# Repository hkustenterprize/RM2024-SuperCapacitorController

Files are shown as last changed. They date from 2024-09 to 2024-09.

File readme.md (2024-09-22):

# 香港科技大学ENTERPRIZE战队
# RM2024超级电容控制器
# 硬件方案&软件方案 完全开源

>设计者：蒋益诚 戎羿
> 
>文档撰写：戎羿

## 文件结构

```
Calibration/cal.xlsx                              ----校准用Excel工具表
Core                                              ----核心代码文件
Docs                                              ----文档附图源码
Drivers                                           ----STM32驱动文件
hardware                                          ----硬件项目文件
      --    SuperCap2024_Control_V1.1R_F3_ISOPWR  ----控制板Kicad项目文件
      --    SuperCap2024_Power_V1.2R              ----功率板Kicad项目文件
Middlewares/ST/ARM/DSP/Inc/arm_math.h             ----数学加速库头文件
.clang-format
.clang-tidy
.cproject
CMakeLists.txt                                    ----由CLion生成的CMake编译文件，便于CLion创建项目
CMakeLists_template.txt
Makefile                                          ----由CubeMX生成的MakeFile编译文件
RM2024-SuperCap-F3-V0.2.ioc                       ----STM32CubeMX项目文件
startup_stm32f334x8.s                             ----由CubeMX生成的启动文件
startup_stm32f334x8_SuperCap.s                    ----由CubeMX生成的启动文件改版，当前使用中
STM32F334R8Tx_FLASH.ld                            ----由CubeMX生成的链接文件
STM32F334R8Tx_SuperCap_FLASH.ld                   ----由CubeMX生成的链接文件改版，当前使用中
SuperCap-F3.mk                                    ----队内通用MakeFile库
```

## 使用方法
###	硬件接口&连接
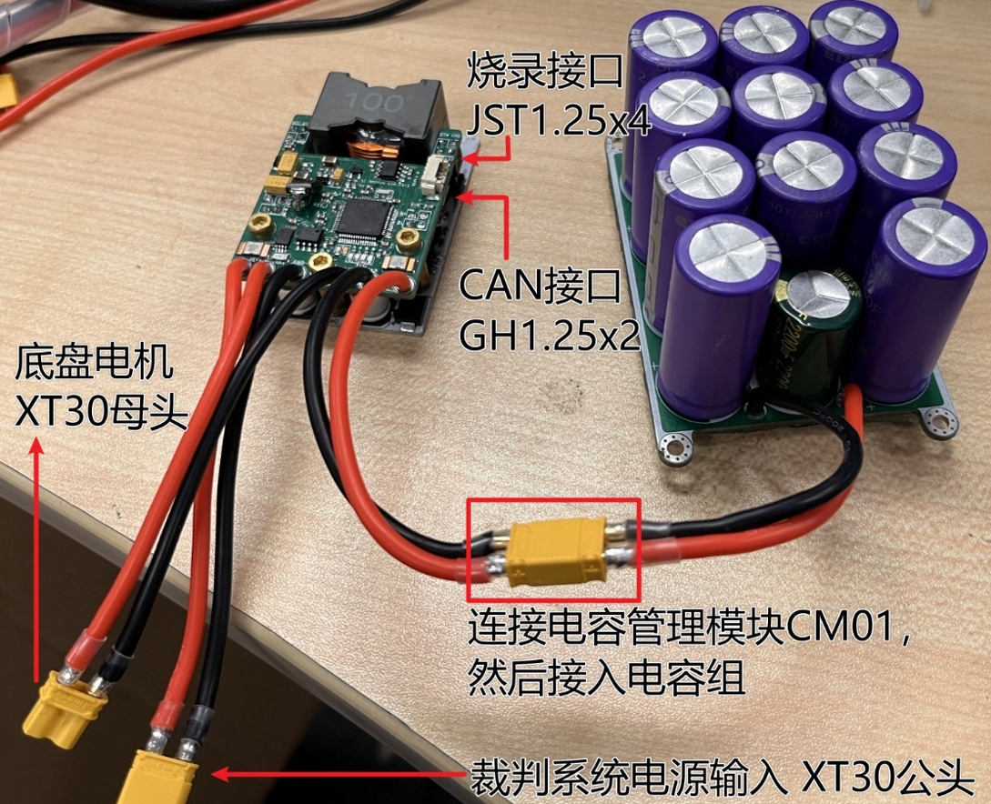
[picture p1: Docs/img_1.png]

###	软件环境&编译&烧录
本项目基于GCC ARM GNU工具链。
1.	安装GCC环境。以Windows系统下为例，下载MSYS2并安装，在系统环境变量中加入相关目录。
2.	安装`arm-none-eabi-gcc`
      然后即可执行编译操作。需要注意编译时需要指定HARDWARE_ID，否则将会报错。

      `make -j HARDWARE_ID=xxx`

      得到`build/`目录下`RM2024-SuperCap-F3-V1R.elf`文件即为编译成功。

      将elf文件在ozone新建项目中打开，即可通过JLink烧录至MCU中。

## 移植兼容性
该项目通过STM32的HAL库实现大部分去耦，方便移植。

用户代码全部位于 `Core/` 中，将相应文件转移到另生成的项目中可以轻松移植。例如专用STM32G474作为开发用MCU。

而部分相对底层的外设代码，例如HRTIM与ADC的配置等，则需要手动修改。

总体而言该项目可移植性较佳。

## 开源报告
可以见于Github Release处

## 开源说明
本项目通过GPL3.0协议开源

## PCB项目说明
硬件部分使用KiCAD设计。

Github上在线预览：使用[KiCanvas](https://kicanvas.org/)

上板原理图：[预览](https://kicanvas.org/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)

上板PCB：[预览](https://kicanvas.org/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)

下板原理图：[预览](https://kicanvas.org/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)

下板PCB：[预览](https://kicanvas.org/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)

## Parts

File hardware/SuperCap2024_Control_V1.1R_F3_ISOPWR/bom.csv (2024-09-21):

Designator | Footprint | Quantity | Value | LCSC Part #
BZ1 | MLT-9032 | 1 | Buzzer-9032
C1, C10, C11, C12, C13, C14, C17, C19, C20, C21, C22, C23, C24, C25, C26, C27, C28, C29, C30, C31, C32, C33, C39, C41, C47, C8 | 0603 | 26 | 100n
C15, C16, C3, C34, C40, C42, C5 | 0603 | 7 | 10u
C18, C36, C37, C44, C45, C49, C50, C52, C53, C54, C55, C9 | 1206 | 12 | 10u
C38, C46 | CP_EIA-6032-28_Kemet-C | 2 | C_Polarized
C4 | 0603 | 1 | 20p
C43 | 0603 | 1 | 10n
C51, C56, C57, C58 | 1206 | 4 | 100u 6.3V
D1, D2, D3 | D_SMF | 3 | DSS34
D10, D11, D19 | D_SMF | 3 | SMF10A
D13, D14, D6, D7, D8, D9 | 0603 | 6 | LED
D22 | D_SMF | 1 | SMF5V0A
D4 | D_SMF | 1 | SMF3.3A
D5 | D_SMA | 1 | SMAJ28A
F1, F2 | 1206 | 2 | 30A
F3, F4 | 1206 | 2 | 1A
FB1 | 1206 | 1 | FerriteBead
FB2 | 0603 | 1 | FerriteBead
H1, H2, H3 | MountingHole_3.2mm_M3_ISO14580_Pad | 3 | MountingHole_Pad
J1, J4 | PinHeader_2x02_P2.54mm_Vertical_SMD | 2 | Conn_02x02_Odd_Even
J2 | JST_GH_SM02B-GHS-TB_1x02-1MP_P1.25mm_Horizontal | 1 | Conn_01x02_MountingPin
J3 | Molex_PicoBlade_53261-0471_1x04-1MP_P1.25mm_Horizontal | 1 | Conn_01x04_MountingPin
J5, J6 | PinHeader_2x02_P2.54mm_Vertical | 2 | Conn_02x02_Odd_Even
L1 | L_Bourns-SRN4018 | 1 | 4.7u
L2 | L_Sunlord_SWPA252012S | 1 | 4.7u
Q1 | SOT-23 | 1 | AO3400A
R1, R2, R22, R23, R24, R26, R27, R3, R37, R4, R5 | 0603 | 11 | 33r
R10, R11, R7, R8 | 0603 | 4 | 2.2k
R12, R15, R9 | 2512 | 3 | 2mr
R13, R14, R30, R31 | 0603 | 4 | 1k
R16, R19 | 0603 | 2 | 90k 25ppm
R17, R20 | 0603 | 2 | 10k 25ppm
R18, R21 | 0603 | 2 | 68r
R25, R36, R38 | 0603 | 3 | 120r
R28, R40, R42, R6 | 0603 | 4 | 10k
R39 | 0603 | 1 | 118k
R41 | 0603 | 1 | 53.6k
TP1, TP2, TP3, TP4, TP5, TP6 | TestPoint_Plated_Hole_D3.0mm | 6 | TestPoint
U1, U3 | BxxxxS-1W | 2 | ISO_DC
U10 | SOT-23-5 | 1 | RS3236
U11, U9 | SOT-23-6 | 2 | RY8411
U2, U4, U5 | TSSOP-8_4.4x3mm_P0.65mm | 3 | INA240A1PW
U6 | SOIC-8_3.9x4.9mm_P1.27mm | 1 | GS8332-SR
U7 | LQFP-64_10x10mm_P0.5mm | 1 | STM32F334R8Tx
U8 | SOIC-8_3.9x4.9mm_P1.27mm | 1 | SIT1042/3
Y1 | Resonator_SMD_Murata_CSTxExxV-3Pin_3.0x1.1mm | 1 | CSTCE8M

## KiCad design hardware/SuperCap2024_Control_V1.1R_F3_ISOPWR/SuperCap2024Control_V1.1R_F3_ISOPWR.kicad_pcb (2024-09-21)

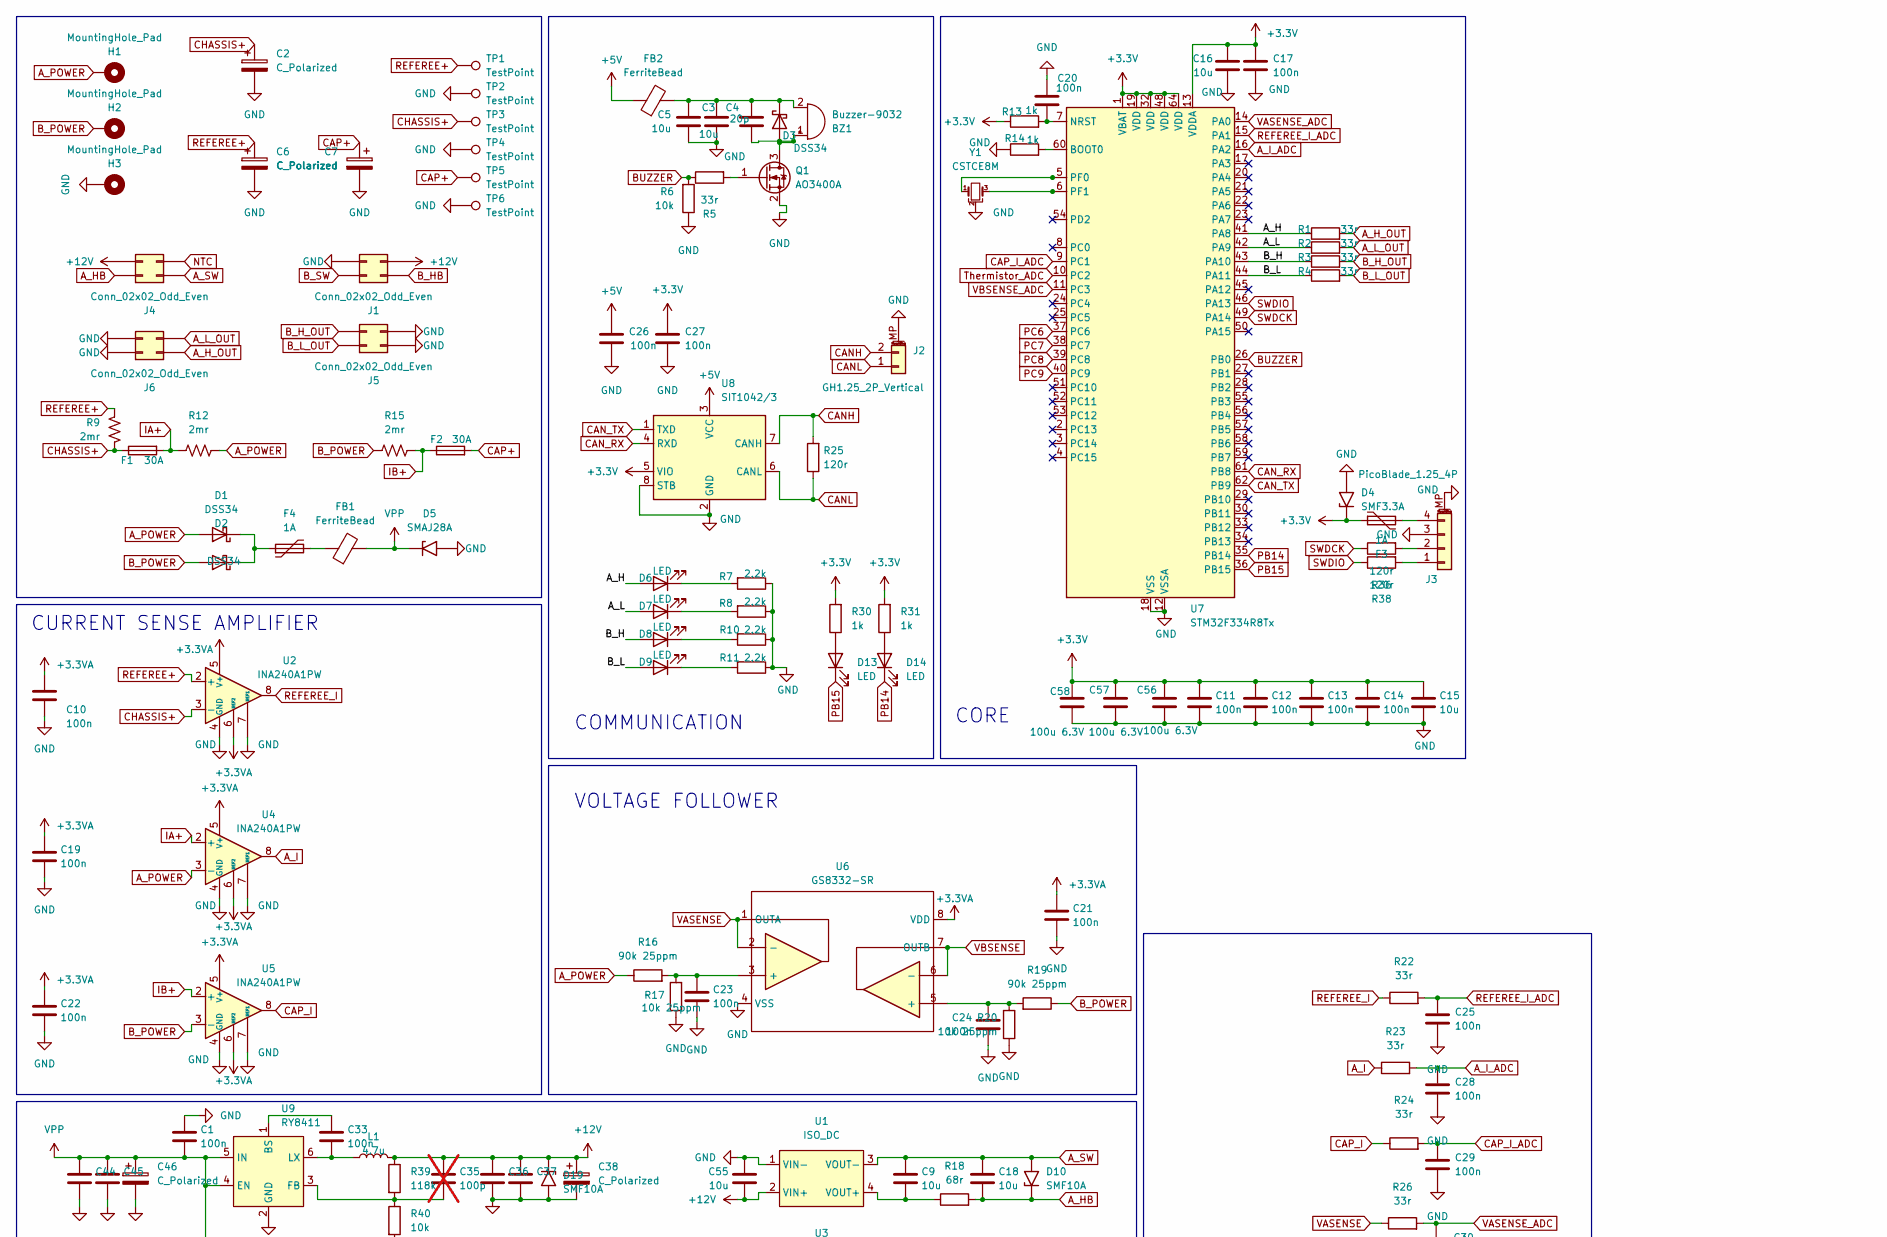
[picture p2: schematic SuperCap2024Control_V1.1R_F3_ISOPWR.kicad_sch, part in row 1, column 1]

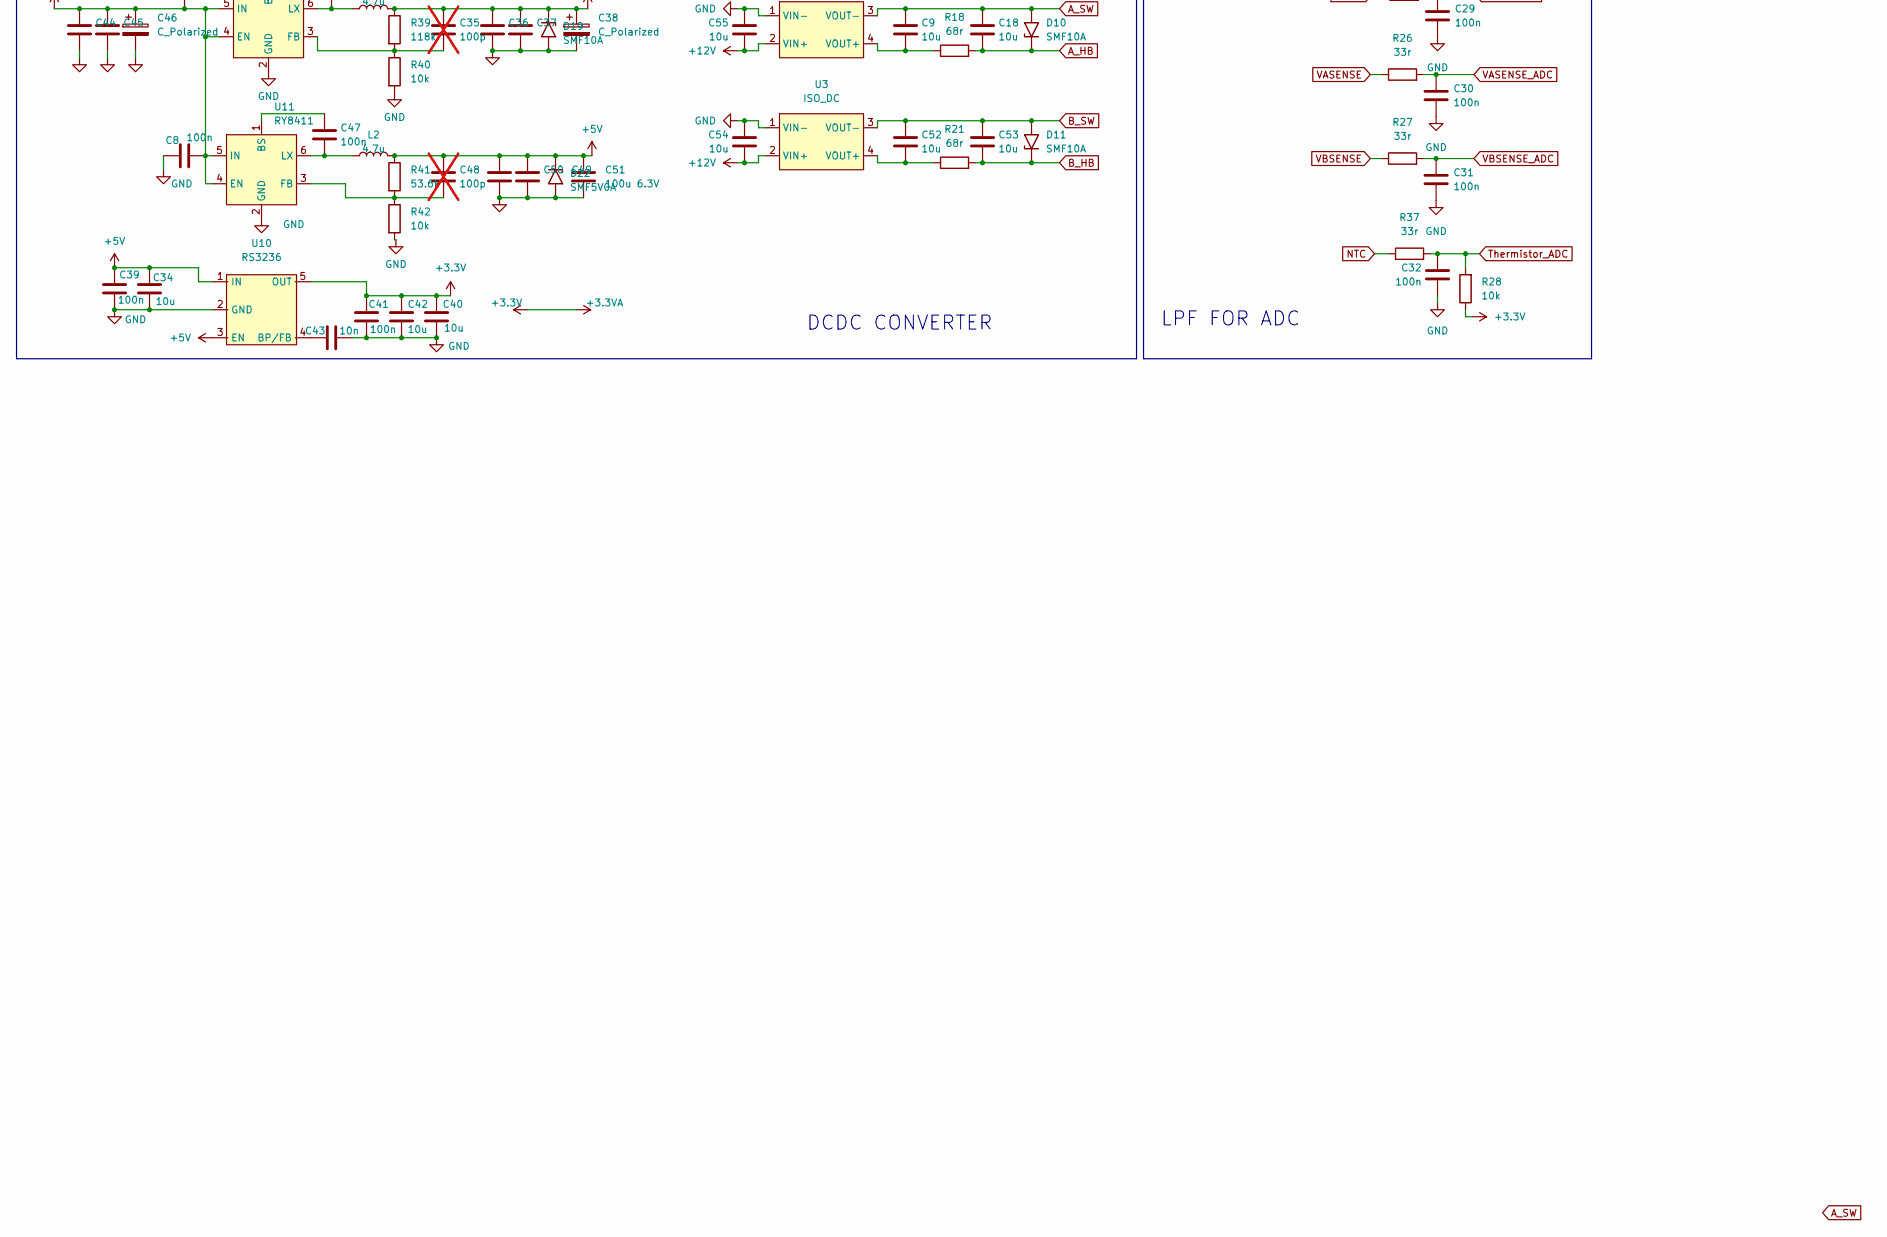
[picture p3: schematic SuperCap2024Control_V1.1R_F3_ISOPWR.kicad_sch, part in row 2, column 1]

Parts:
BZ1: Buzzer-9032; MLT-9032
C1, C8, C10, C11, C12, C13, C14, C17, C19, C20, C21, C22, C23, C24, C25, C26, C27, C28, C29, C30, C31, C32, C33, C39, C41, C47: 100n; C_0603_1608Metric
C2, C6, C7: C_Polarized; CP_Radial_D8.0mm_P3.50mm
C3, C5, C15, C16, C34, C40, C42: 10u; C_0603_1608Metric
C4: 20p; C_0603_1608Metric
C9, C18, C36, C37, C44, C45, C49, C50, C52, C53, C54, C55: 10u; C_1206_3216Metric
C35, C48: 100p; C_0603_1608Metric; not fitted
C38, C46: C_Polarized; CP_EIA-6032-28_Kemet-C
C43: 10n; C_0603_1608Metric
C51, C56, C57, C58: 100u 6.3V; C_1206_3216Metric
D1, D2, D3: DSS34; D_SMF
D4: SMF3.3A; D_SMF
D5: SMAJ28A; D_SMA
D6, D7, D8, D9, D13, D14: LED; LED_0603_1608Metric
D10, D11, D19: SMF10A; D_SMF
D22: SMF5V0A; D_SMF
F1, F2: 30A; Fuse_1206_3216Metric
F3, F4: 1A; Fuse_1206_3216Metric
FB1: FerriteBead; L_1206_3216Metric
FB2: FerriteBead; L_0603_1608Metric
H1, H2, H3: MountingHole_Pad; MountingHole_3.2mm_M3_ISO14580_Pad
J1, J4: Conn_02x02_Odd_Even; PinHeader_2x02_P2.54mm_Vertical_SMD
J2: GH1.25_2P_Vertical; JST_GH_SM02B-GHS-TB_1x02-1MP_P1.25mm_Horizontal
J3: PicoBlade_1.25_4P; Molex_PicoBlade_53261-0471_1x04-1MP_P1.25mm_Horizontal
J5, J6: Conn_02x02_Odd_Even; PinHeader_2x02_P2.54mm_Vertical
L1: 4.7u; L_Bourns-SRN4018
L2: 4.7u; L_Sunlord_SWPA252012S
Q1: AO3400A; SOT-23
R1, R2, R3, R4, R5, R22, R23, R24, R26, R27, R37: 33r; R_0603_1608Metric
R6, R28, R40, R42: 10k; R_0603_1608Metric
R7, R8, R10, R11: 2.2k; R_0603_1608Metric
R9, R12, R15: 2mr; R_2512_6332Metric
R13, R14, R30, R31: 1k; R_0603_1608Metric
R16, R19: 90k 25ppm; R_0603_1608Metric
R17, R20: 10k 25ppm; R_0603_1608Metric
R18, R21: 68r; R_0603_1608Metric
R25, R36, R38: 120r; R_0603_1608Metric
R39: 118k; R_0603_1608Metric
R41: 53.6k; R_0603_1608Metric
TP1, TP2, TP3, TP4, TP5, TP6: TestPoint; TestPoint_Plated_Hole_D3.0mm
U1, U3: ISO_DC; BxxxxS-1W
U2, U4, U5: INA240A1PW; TSSOP-8_4.4x3mm_P0.65mm
U6: GS8332-SR; SOIC-8_3.9x4.9mm_P1.27mm
U7: STM32F334R8Tx; LQFP-64_10x10mm_P0.5mm
U8: SIT1042/3; SOIC-8_3.9x4.9mm_P1.27mm
U9, U11: RY8411; SOT-23-6
U10: RS3236; SOT-23-5
Y1: CSTCE8M; Resonator_SMD_Murata_CSTxExxV-3Pin_3.0x1.1mm

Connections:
+3.3V: C10.1, C11.1, C12.1, C13.1, C14.1, C15.1, C16.2, C17.2, C19.1, C21.1, C22.1, C27.2, C40.1, C41.1, C42.1, C56.1, C57.1, C58.1, D4.1 (A1), F3.1, R13.1, R28.1, R30.2, R31.2, U2.5 (V+), U2.6 (REF2), U4.5 (V+), U4.6 (REF2), U5.5 (V+), U5.6 (REF2), U6.8 (VDD), U7.1 (VBAT), U7.13 (VDDA), U7.19 (VDD), U7.32 (VDD), U7.48 (VDD), U7.64 (VDD), U8.5 (VIO), U10.5 (OUT)
+5V: C26.2, C34.1, C39.1, C48.1, C49.1, C50.1, C51.1, D22.1 (A1), FB2.1, L2.2, R41.1, U8.3 (VCC), U10.1 (IN), U10.3 (EN)
+12V: C35.1, C36.1, C37.1, C38.1, C54.2, C55.2, D19.1 (A1), J1.4, J4.3, L1.2, R39.1, U1.2 (VIN+), U3.2 (VIN+)
/A_H: D6.2 (A), R1.1, U7.41 (PA8)
/A_L: D7.2 (A), R2.1, U7.42 (PA9)
/B_H: D8.2 (A), R3.1, U7.43 (PA10)
/B_L: D9.2 (A), R4.1, U7.44 (PA11)
A_HB: C18.2, D10.1 (A1), J4.1, R18.2
A_H_OUT: J6.2, R1.2
A_I: R23.1, U4.8
A_I_ADC: C28.2, R23.2, U7.16 (PA2)
A_L_OUT: J6.4, R2.2
A_POWER: D1.2 (A), H1.1, R12.2, R16.1, U4.3 (-)
A_SW: C9.1, C18.1, D10.2 (A2), J4.2, U1.3 (VOUT-)
BUZZER: R5.1, R6.2, U7.26 (PB0)
B_HB: C53.2, D11.1 (A1), J1.2, R21.2
B_H_OUT: J5.3, R3.2
B_L_OUT: J5.1, R4.2
B_POWER: D2.2 (A), H2.1, R15.1, R19.1, U5.3 (-)
B_SW: C52.1, C53.1, D11.2 (A2), J1.1, U3.3 (VOUT-)
CANH: J2.2, R25.2, U8.7 (CANH)
CANL: J2.1, R25.1, U8.6 (CANL)
CAN_RX: U7.61 (PB8), U8.4 (RXD)
CAN_TX: U7.62 (PB9), U8.1 (TXD)
CAP+: C7.1, F2.2, TP5.1
CAP_I: R24.1, U5.8
CAP_I_ADC: C29.2, R24.2, U7.9 (PC1)
CHASSIS+: C2.1, F1.1, R9.2, TP3.1, U2.3 (-)
GND: C1.1, C2.2, C3.1, C5.1, C6.2, C7.2, C8.2, C10.2, C11.2, C12.2, C13.2, C14.2, C15.2, C16.1, C17.1, C19.2, C20.2, C21.2, C22.2, C23.2, C24.2, C25.1, C26.1, C27.1, C28.1, C29.1, C30.1, C31.1, C32.2, C34.2, C36.2, C37.2, C38.2, C39.2, C40.2, C41.2, C42.2, C43.2, C44.2, C45.2, C46.2, C49.2, C50.2, C51.2, C54.1, C55.1, C56.2, C57.2, C58.2, D4.2 (A2), D5.2 (A2), D19.2 (A2), D22.2 (A2), H3.1, J1.3, J2.MP (MountPin), J3.3, J3.MP (MountPin), J5.2, J5.4, J6.1, J6.3, Q1.2 (S), R6.1, R7.1, R8.1, R10.1, R11.1, R14.1, R17.1, R20.1, R40.2, R42.2, TP2.1, TP4.1, TP6.1, U1.1 (VIN-), U2.1 (GND), U2.4 (GND), U2.7 (REF1), U3.1 (VIN-), U4.1 (GND), U4.4 (GND), U4.7 (REF1), U5.1 (GND), U5.4 (GND), U5.7 (REF1), U6.4 (VSS), U7.12 (VSSA), U7.18 (VSS), U7.31 (VSS), U7.47 (VSS), U7.63 (VSS), U8.2 (GND), U8.8 (STB), U9.2 (GND), U10.2 (GND), U11.2 (GND), Y1.2
IA+: F1.2, R12.1, U4.2 (+)
IB+: F2.1, R15.2, U5.2 (+)
NTC: J4.4, R37.1
unnamed: BZ1.2 (+), C3.2, C4.2, C5.2, D3.1 (K), FB2.2
unnamed: BZ1.1 (-), C4.1, D3.2 (A), Q1.3 (D)
unnamed: C23.1, R16.2, R17.2, U6.3 (+)
unnamed: C24.1, R19.2, R20.2, U6.5 (+)
unnamed: D1.1 (K), D2.1 (K), F4.1
unnamed: D6.1 (K), R7.2
unnamed: D7.1 (K), R8.2
unnamed: D8.1 (K), R10.2
unnamed: D9.1 (K), R11.2
unnamed: D13.2 (A), R30.1
unnamed: D14.2 (A), R31.1
unnamed: F4.2, FB1.1
unnamed: J3.1, R38.2
unnamed: J3.2, R36.2
unnamed: F3.2, J3.4
unnamed: Q1.1 (G), R5.2
unnamed: C9.2, R18.1, U1.4 (VOUT+)
unnamed: C52.2, R21.1, U3.4 (VOUT+)
unnamed: R14.2, U7.60 (BOOT0)
unnamed: C20.1, R13.2, U7.7 (NRST)
unnamed: U7.5 (PF0), Y1.1
unnamed: U7.6 (PF1), Y1.3
unnamed: C33.1, U9.1 (BS)
unnamed: C35.2, R39.2, R40.1, U9.3 (FB)
unnamed: C33.2, L1.1, U9.6 (LX)
unnamed: C43.1, U10.4 (BP/FB)
unnamed: C47.1, U11.1 (BS)
unnamed: C48.2, R41.2, R42.1, U11.3 (FB)
unnamed: C47.2, L2.1, U11.6 (LX)
PB14: D14.1 (K), U7.35 (PB14)
PB15: D13.1 (K), U7.36 (PB15)
PC6: U7.37 (PC6)
PC7: U7.38 (PC7)
PC8: U7.39 (PC8)
PC9: U7.40 (PC9)
REFEREE+: C6.1, R9.1, TP1.1, U2.2 (+)
REFEREE_I: R22.1, U2.8
REFEREE_I_ADC: C25.2, R22.2, U7.15 (PA1)
SWDCK: R36.1, U7.49 (PA14)
SWDIO: R38.1, U7.46 (PA13)
Thermistor_ADC: C32.1, R28.2, R37.2, U7.10 (PC2)
VASENSE: R26.1, U6.1 (OUTA), U6.2 (-)
VASENSE_ADC: C30.2, R26.2, U7.14 (PA0)
VBSENSE: R27.1, U6.6 (-), U6.7 (OUTB)
VBSENSE_ADC: C31.2, R27.2, U7.11 (PC3)
VPP: C1.2, C8.1, C44.1, C45.1, C46.1, D5.1 (A1), FB1.2, U9.4 (EN), U9.5 (IN), U11.4 (EN), U11.5 (IN)

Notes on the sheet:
COMMUNICATION
CURRENT SENSE AMPLIFIER
CORE
DCDC CONVERTER
VOLTAGE FOLLOWER
LPF FOR ADC

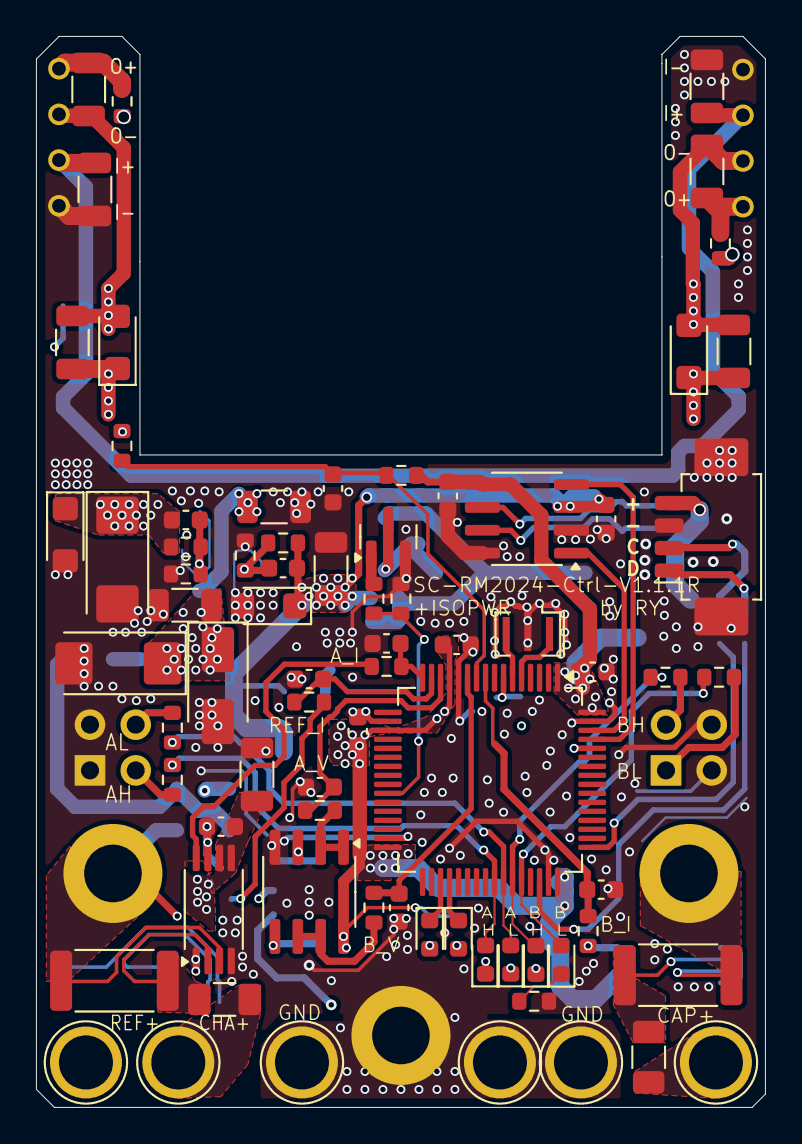
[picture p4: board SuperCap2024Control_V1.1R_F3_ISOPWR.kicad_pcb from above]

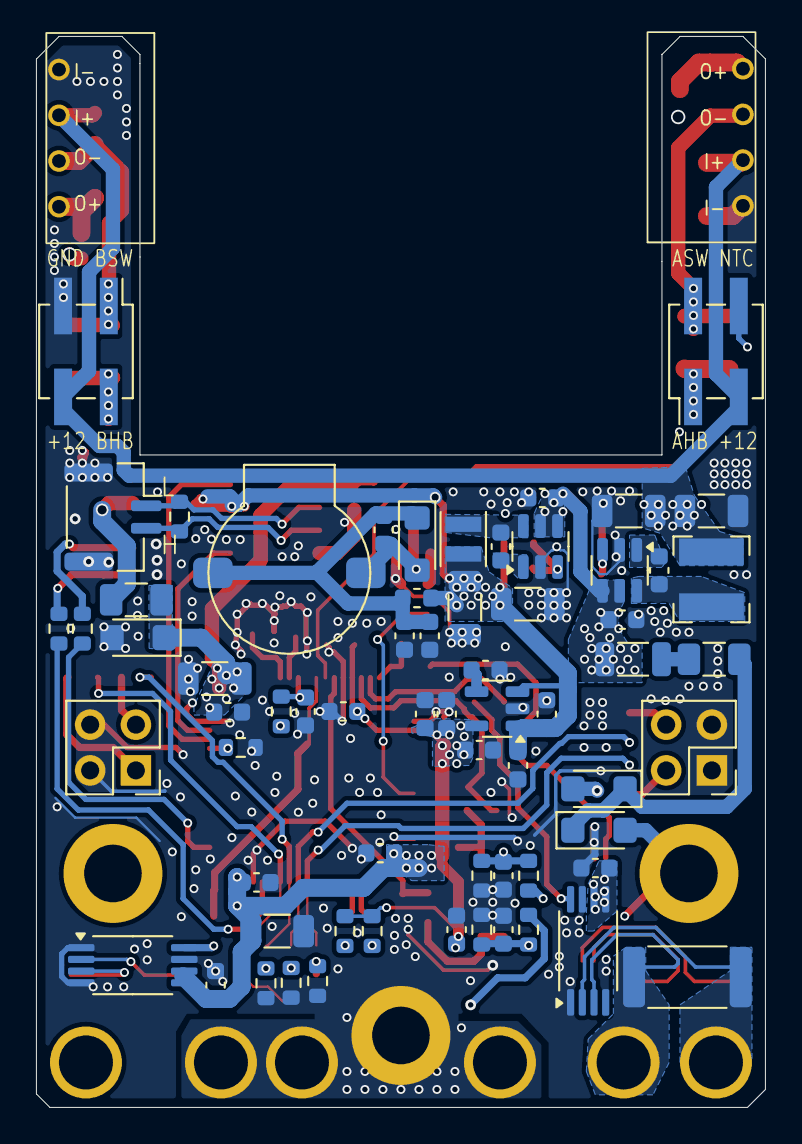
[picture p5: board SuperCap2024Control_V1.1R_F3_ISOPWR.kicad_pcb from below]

Board: 4 copper layers, 40.5 x 59.5 mm, 144 parts (67 on the bottom side), 74 nets.

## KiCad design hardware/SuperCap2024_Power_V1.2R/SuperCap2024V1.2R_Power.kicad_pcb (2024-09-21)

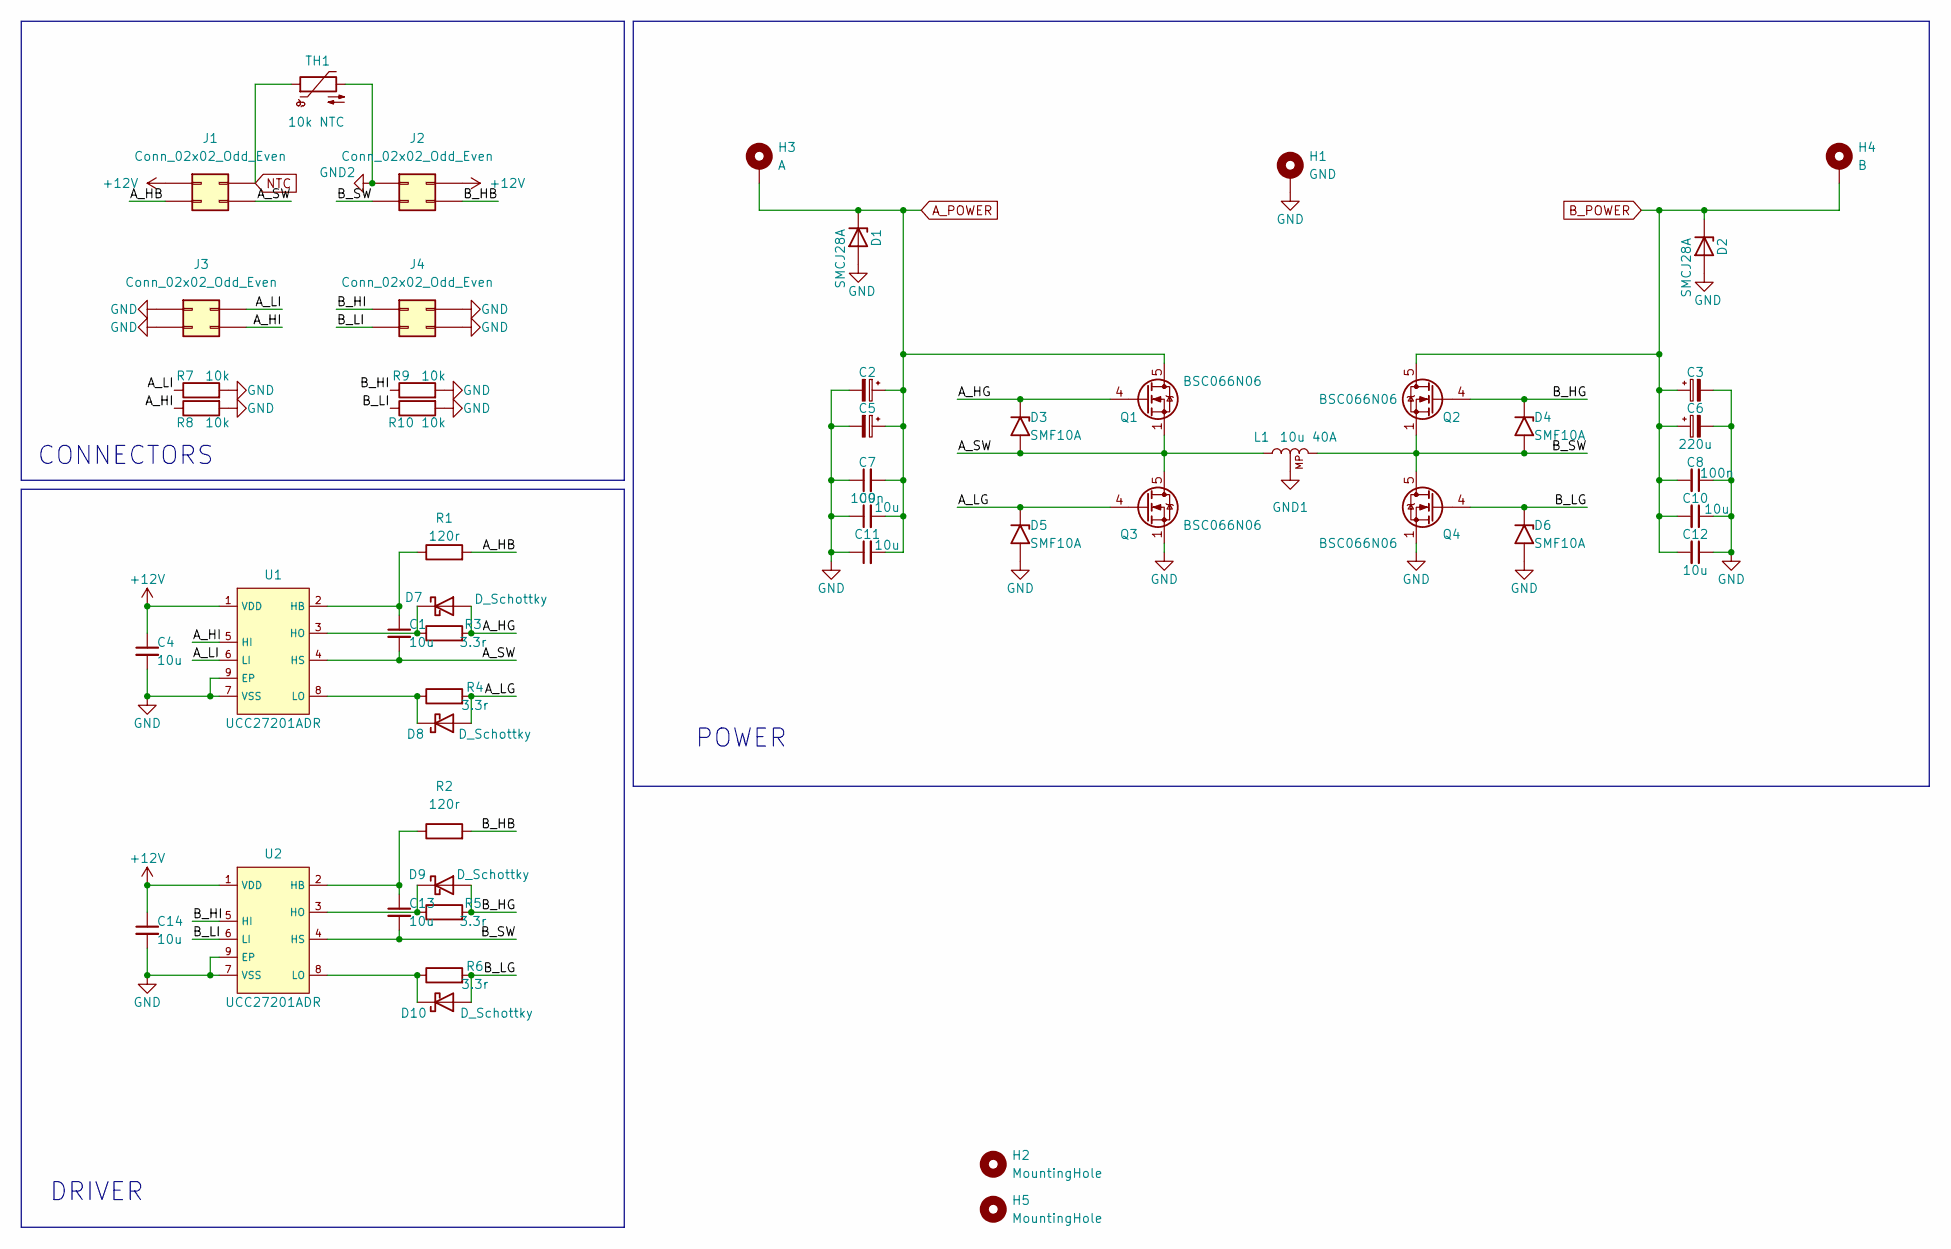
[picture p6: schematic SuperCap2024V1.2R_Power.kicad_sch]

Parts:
C1, C13: 10u; C_0603_1608Metric
C2, C3, C5, C6: 220u; CP_Elec_8x10
C4, C9, C10, C11, C12, C14: 10u; C_1206_3216Metric
C7, C8: 100n; C_0603_1608Metric
D1, D2: SMCJ28A; D_SMC
D3, D4, D5, D6: SMF10A; D_SOD-123F
D7, D8, D9, D10: D_Schottky; D_SOD-123F
H1: GND; TestPoint_Pad_D4.0mm
H2, H5: MountingHole; MountingHole_3.2mm_M3
H3: A; TestPoint_Pad_D4.0mm
H4: B; TestPoint_Pad_D4.0mm
J1, J2, J3, J4: Conn_02x02_Odd_Even; PinHeader_2x02_P2.54mm_Vertical_SMD
L1: 10u 40A; PQ2617BHA
Q1, Q2, Q3, Q4: BSC066N06; TDSON-8-1_HandSolder
R1, R2: 120r; R_1206_3216Metric
R3, R4, R5, R6: 3.3r; R_0603_1608Metric
R7, R8, R9, R10: 10k; R_0603_1608Metric
TH1: 10k NTC; R_1206_3216Metric
U1, U2: UCC27201ADR; SOP-8_3.9x4.9mm_P1.27mm

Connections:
+12V: C4.1, C14.1, J1.1, J2.2, U1.1 (VDD), U2.1 (VDD)
/A_HB: J1.3, R1.2
/A_HG: D3.1 (A1), D7.2 (A), Q1.4 (G), R3.2
/A_HI: J3.4, R8.1, U1.5 (HI)
/A_LG: D5.1 (A1), D8.2 (A), Q3.4 (G), R4.2
/A_LI: J3.2, R7.1, U1.6 (LI)
/A_SW: C1.2, D3.2 (A2), J1.4, L1.1, Q1.1 (S), Q1.2 (S), Q1.3 (S), Q3.5 (D), U1.4 (HS)
/B_HB: J2.4, R2.2
/B_HG: D4.1 (A1), D9.2 (A), Q2.4 (G), R5.2
/B_HI: J4.1, R9.1, U2.5 (HI)
/B_LG: D6.1 (A1), D10.2 (A), Q4.4 (G), R6.2
/B_LI: J4.3, R10.1, U2.6 (LI)
/B_SW: C13.2, D4.2 (A2), J2.3, L1.2, Q2.1 (S), Q2.2 (S), Q2.3 (S), Q4.5 (D), U2.4 (HS)
A_POWER: C2.1, C5.1, C7.2, C9.2, C11.2, D1.1 (K), H3.1, Q1.5 (D)
B_POWER: C3.1, C6.1, C8.2, C10.2, C12.2, D2.1 (K), H4.1, Q2.5 (D)
GND: C2.2, C3.2, C4.2, C5.2, C6.2, C7.1, C8.1, C9.1, C10.1, C11.1, C12.1, C14.2, D1.2 (A), D2.2 (A), D5.2 (A2), D6.2 (A2), H1.1, J3.1, J3.3, J4.2, J4.4, Q3.1 (S), Q3.2 (S), Q3.3 (S), Q4.1 (S), Q4.2 (S), Q4.3 (S), R7.2, R8.2, R9.2, R10.2, U1.7 (VSS), U1.9 (EP), U2.7 (VSS), U2.9 (EP)
GND1: L1.3 (MP)
GND2: J2.1, TH1.2
NTC: J1.2, TH1.1
unnamed: C1.1, R1.1, U1.2 (HB)
unnamed: D7.1 (K), R3.1, U1.3 (HO)
unnamed: D8.1 (K), R4.1, U1.8 (LO)
unnamed: C13.1, R2.1, U2.2 (HB)
unnamed: D9.1 (K), R5.1, U2.3 (HO)
unnamed: D10.1 (K), R6.1, U2.8 (LO)

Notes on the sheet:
POWER
DRIVER
CONNECTORS

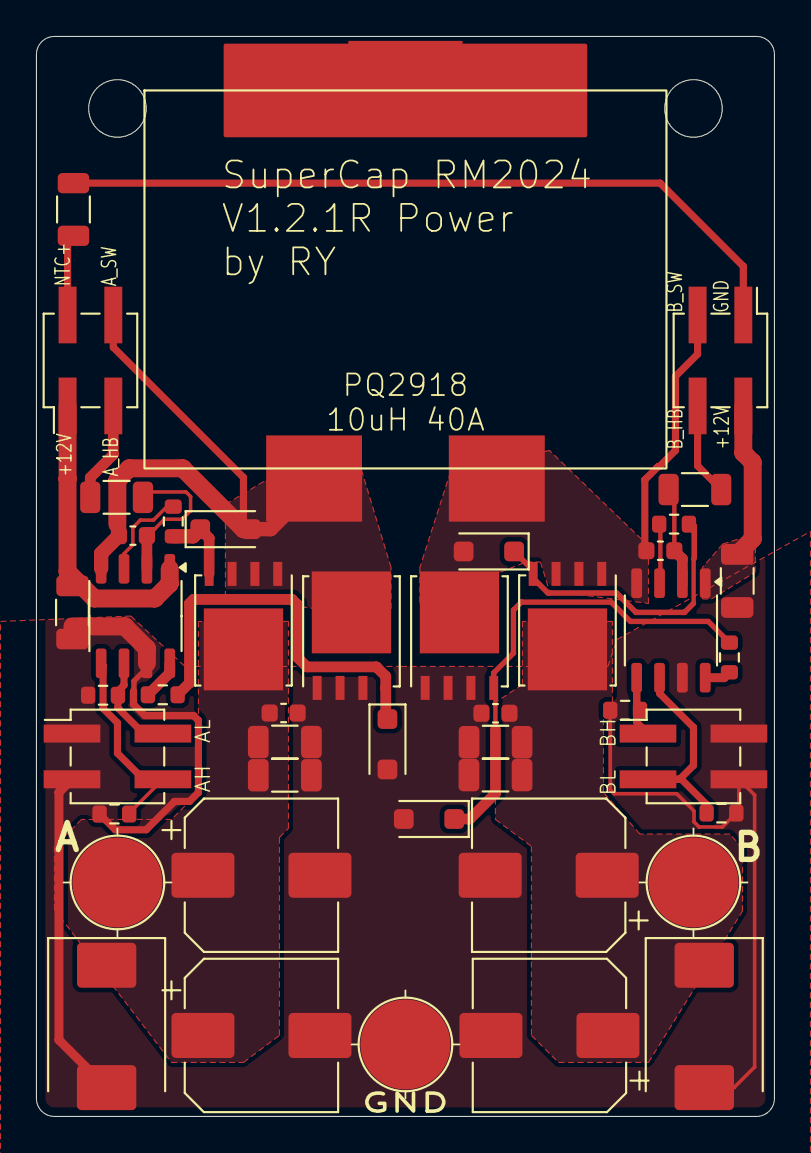
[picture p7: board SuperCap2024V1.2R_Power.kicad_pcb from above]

Board: 2 copper layers, 41.0 x 60.0 mm, 47 parts (0 on the bottom side), 24 nets.

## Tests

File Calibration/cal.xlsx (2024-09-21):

 | real data |  | adc value |  | k | b
VASide | 12 | 24 | 1483 | 2969 | 0.008075370121 | 0.02422611036
VBSide | 12 | 28.8 | 1477 | 3552 | 0.008096385542 | 0.04163855422
IAConvert | 1 | 8 | 1995.4 | 1648.7 | -0.02019036631 | 41.28785694
Ijudge | 1 | 8 | 1994.3 | 1647.9 | -0.02020785219 | 41.30051963
IBConvert | 1 | 8 | 1994.6 | 1648.4 | -0.02021952629 | 41.32986713
 |  |  |  |  | #DIV/0! | #DIV/0!
 |  |  |  |  | #DIV/0! | #DIV/0!
 |  |  |  |  | #DIV/0! | #DIV/0!
 |  |  |  |  | #DIV/0! | #DIV/0!
 |  |  |  |  | #DIV/0! | #DIV/0!
 |  |  |  |  | #DIV/0! | #DIV/0!
 |  |  |  |  | #DIV/0! | #DIV/0!

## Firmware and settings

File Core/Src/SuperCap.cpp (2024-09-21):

/**
 * @file SuperCap.cpp
 * @author JIANG Yicheng RM2023
 * @brief
 * @version 0.1
 * @date 2023-01-22
 *
 * @copyright Copyright (c) 2023
 */

#include "Buzzer.hpp"
#include "Calibration.hpp"
#include "Communication.hpp"
#include "Config.hpp"
#include "PowerManager.hpp"
#include "iwdg.h"
#include "main.h"

namespace SuperCap
{
static void loop()
{
    while (true)
    {
        __HAL_IWDG_RELOAD_COUNTER(&hiwdg);
        HAL_Delay(1);
    }
}

void configIWDG()
{
    hiwdg.Instance = IWDG;
    __HAL_IWDG_START(&hiwdg);
    IWDG_ENABLE_WRITE_ACCESS(&hiwdg);
    hiwdg.Instance->PR  = IWDG_PRESCALER_4;
    hiwdg.Instance->RLR = 1000;
    while ((hiwdg.Instance->SR & (IWDG_SR_WVU | IWDG_SR_RVU | IWDG_SR_PVU)) != 0x00u)
        ;
    __HAL_IWDG_RELOAD_COUNTER(&hiwdg);
}

void init()
{
    HAL_Delay(200);  // wait voltage stabilization

    /* initialize communication */
    Buzzer::init();

    /* check hardware id */
    static volatile uint32_t hardwareID = 0;

    hardwareID = HAL_FLASHEx_OBGetUserData(OB_DATA_ADDRESS_DATA0);

    if (hardwareID != (uint32_t)HARDWARE_ID)
    {
#ifdef CALIBRATION_MODE
        while (HAL_FLASH_OB_Unlock() != HAL_OK)  // unlock flash option bytes
            __ASM volatile("bkpt ");

        while (HAL_FLASHEx_OBErase() != HAL_OK)  // erase option bytes
            __ASM volatile("bkpt ");

        FLASH_OBProgramInitTypeDef pOBInit;
        pOBInit.OptionType  = OPTIONBYTE_WRP | OPTIONBYTE_RDP | OPTIONBYTE_USER | OPTIONBYTE_DATA;
        pOBInit.WRPState    = OB_WRPSTATE_DISABLE;
        pOBInit.WRPPage     = 0xFFFFFFFF;
        pOBInit.RDPLevel    = OB_RDP_LEVEL_0;
        pOBInit.USERConfig  = OB_IWDG_SW | OB_STOP_NO_RST | OB_STDBY_NO_RST | OB_BOOT1_RESET | OB_VDDA_ANALOG_ON | OB_SRAM_PARITY_RESET;
        pOBInit.DATAAddress = OB_DATA_ADDRESS_DATA0;
        pOBInit.DATAData    = (uint8_t)HARDWARE_ID;        // set hardware id

        while (HAL_FLASHEx_OBProgram(&pOBInit) != HAL_OK)  // program option bytes
            __ASM volatile("bkpt ");

        while (HAL_FLASH_OB_Lock() != HAL_OK)  // lock flash option bytes
            __ASM volatile("bkpt ");

        while (HAL_FLASH_OB_Launch() != HAL_OK)  // launch option bytes
            __ASM volatile("bkpt ");

#endif
        Buzzer::play(1000);
        while (true)
            __ASM volatile("bkpt ");
    }

    /* initialize power manager */
    Buzzer::play(800, 500);

    Communication::init();

    HAL_Delay(600);

    PowerManager::init();

    configIWDG();
}

extern "C"
{
    void systemStart()
    {
        SuperCap::init();
        loop();
    }
}
}  // namespace SuperCap

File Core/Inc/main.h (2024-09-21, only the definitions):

#define I_SENSE_CAP_Pin GPIO_PIN_1
#define I_SENSE_CAP_GPIO_Port GPIOC
#define SENSE_THERMAL_Pin GPIO_PIN_2
#define SENSE_THERMAL_GPIO_Port GPIOC
#define V_SENSE_B_Pin GPIO_PIN_3
#define V_SENSE_B_GPIO_Port GPIOC
#define V_SENSE_A_Pin GPIO_PIN_0
#define V_SENSE_A_GPIO_Port GPIOA
#define I_SENSE_JUDGE_Pin GPIO_PIN_1
#define I_SENSE_JUDGE_GPIO_Port GPIOA
#define I_SENSE_A_Pin GPIO_PIN_2
#define I_SENSE_A_GPIO_Port GPIOA
#define TIM1_CH2N_BUZZER_Pin GPIO_PIN_0
#define TIM1_CH2N_BUZZER_GPIO_Port GPIOB
#define MOS_A_H_Pin GPIO_PIN_8
#define MOS_A_H_GPIO_Port GPIOA
#define MOS_A_L_Pin GPIO_PIN_9
#define MOS_A_L_GPIO_Port GPIOA
#define MOS_B_H_Pin GPIO_PIN_10
#define MOS_B_H_GPIO_Port GPIOA
#define MOS_B_L_Pin GPIO_PIN_11
#define MOS_B_L_GPIO_Port GPIOA

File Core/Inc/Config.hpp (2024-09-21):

/**
 * @file Config.hpp
 * @author JIANG Yicheng RM2023
 * @brief
 * @version 0.1
 * @date 2023-01-23
 *
 * @copyright Copyright (c) 2023
 */

#define MAX_CAP_VOLTAGE 28.8f

#define SHORT_CIRCUIT_CURRENT 15.5f
#define SHORT_CIRCUIT_VOLTAGE 4.0f

#define I_LIMIT 22.5f

#define OVER_TEMP_TRIGGER_THRESHOLD 180
#define OVER_TEMP_RECOVER_THRESHOLD 200

#define LOW_BATTERY_VOLTAGE 20.92f
#define LOW_BATTERY_RECOVER_VOLTAGE 21.6f

#define DEFAULT_REFEREE_POWER 37.0f

#define ENERGY_BUFFER 50.0f

#define ADC_CHANNEL_COUNT 3
#define ADC_SAMPLE_COUNT 8
#define DIVIDED_BY_ADC_SAMPLE_COUNT (1.0f / ADC_SAMPLE_COUNT)

#define ADC_FILTER_ALPHA 0.5f

#define HRTIM_PERIOD 16000

#pragma once

#define configASSERT(x) \
    if (!(x))           \
        __asm volatile("bkpt ");

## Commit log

2024-09-21 Git History Cleared: Init
    [SuperCap2024Control_V1.1R_F3_ISOPWR.kicad_pcb, SuperCap2024Control_V1.1R_F3_ISOPWR.kicad_sch, SuperCap2024V1.2R_Power.kicad_pcb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]
2024-09-22 Add PCB preview in readme.md
2024-11-09 Fix on incorrect reference to processedSampleData in CALIBRATION_MODE
    [PowerManager.cpp]

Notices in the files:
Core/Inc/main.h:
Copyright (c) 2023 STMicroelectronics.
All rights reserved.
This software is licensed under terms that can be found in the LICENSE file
